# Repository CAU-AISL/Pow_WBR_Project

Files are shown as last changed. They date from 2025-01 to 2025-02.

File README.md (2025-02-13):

# WBR Control
**Wheeled Bipedal Robot POW** project for Capstone Design graduation thesis conducted. This project is inspired by [Ascento](https://www.youtube.com/@AscentoRobotics). @SeungbinOh, Jungbin Park, @Woodaengtang are contributors of this project. 

## Introduction
- This repository is including **ESP32 control** and **MATLAB simulation** code for wheeled bipedal robot POW.
- For robust behavior, balancing, velocity, yaw rate control were conducted using **LQR(Linear Quadratic Regulator)**.
- Discrete LQR gains were calculated offline with 10mm height interval.
- During HILS, LQR gain is determined using linear interpolation according to desired height.

## Library dependencies
- **ESP32 Board**
    - [arduino-esp32](https://github.com/espressif/arduino-esp32): 4D Systems gen4-ESP32 16MB Modules (ESP32-S3R8n16)
    - [Eigen](https://github.com/hideakitai/ArduinoEigen)
    - [Bolder Flight Systems SUBS](https://github.com/bolderflight/sbus)
    - [ESP32Servo](https://madhephaestus.github.io/ESP32Servo/annotated.html)

## Future scope of WBR
- **Backlash issues**
- **Autonomous driving**
- **Enhance estimation**
- **Task variation**
- **Upgrading hardware**
- **Extendable research topics**
    - Optimization based control
    - Reinforcement learning control
    - Autonomous navigation, SLAM
    - System ID - SINDy, Digital twin
    - Estimation in saturated measurement(Tobit Kalman filter)

## Hardware

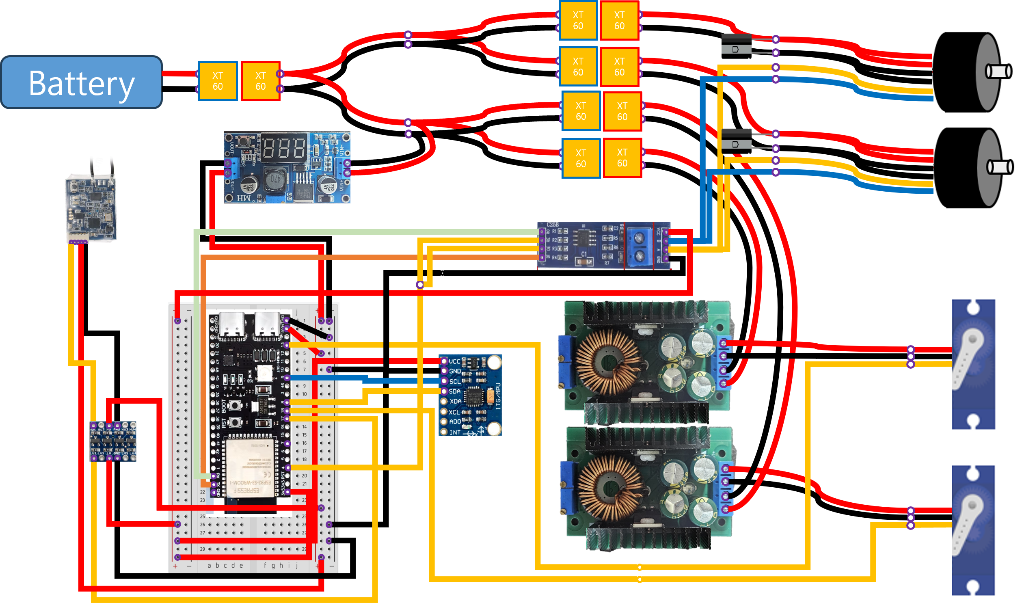
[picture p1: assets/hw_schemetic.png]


- [DCDC step down converter](https://ko.aliexpress.com/item/1005006295829518.html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)
- [DC-DC buck converter](https://ko.aliexpress.com/item/1005001711248152.html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)
- [ESP32 N16R8](https://ko.aliexpress.com/item/1005006002965361.html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) : Please do not use pin number 19 and 20. **Using 19, 20 pin causes serial monitor disconnection.**
- [Hip servo motor](https://ko.aliexpress.com/item/1005006086271452.html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)
- [Wheel motor](https://ko.aliexpress.com/item/1005006136735214.html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)
- [RC Receiver](https://ko.aliexpress.com/item/1005006821905179.html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)
- [MPU6050](https://ko.aliexpress.com/item/1005006579363624.html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)
- [TTL to RS485 converter](https://www.coupang.com/vp/products/104771330?itemId=317638085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)
- [Level shifter](https://www.coupang.com/vp/products/257783456?itemId=808722571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)

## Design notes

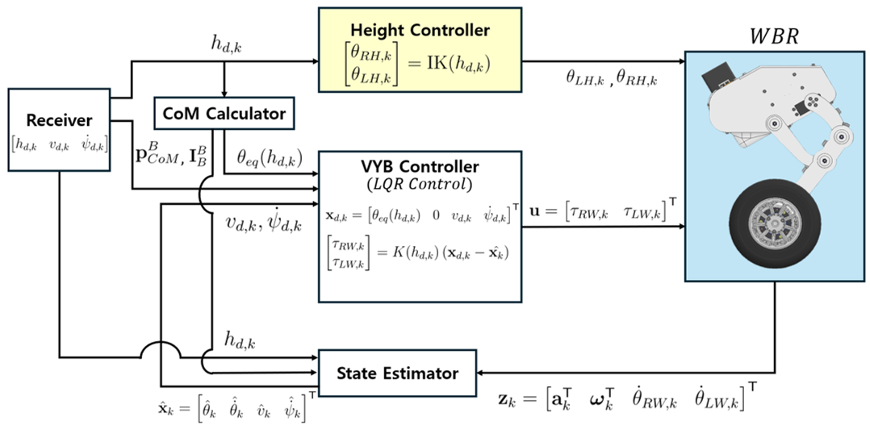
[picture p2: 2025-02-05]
assets/control_diagram.png

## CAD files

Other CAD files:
MATLAB/Linkage_Design/OldVersions/base.0001.ipt
MATLAB/Linkage_Design/OldVersions/link_l1.0001.ipt
MATLAB/Linkage_Design/OldVersions/link_l2.0001.ipt
MATLAB/Linkage_Design/OldVersions/link_l34.0001.ipt
MATLAB/Linkage_Design/OldVersions/linkage_system_sketch.0005.ipt
MATLAB/Linkage_Design/OldVersions/linkage_system_sketch_reference.0002.ipt
MATLAB/Linkage_Design/base.ipt
MATLAB/Linkage_Design/link_l1.ipt
MATLAB/Linkage_Design/link_l2.ipt
MATLAB/Linkage_Design/link_l34.ipt
MATLAB/Linkage_Design/linkage_system_sketch.ipt
MATLAB/Linkage_Design/linkage_system_sketch_reference.ipt
MATLAB/Linkage_Design/linkage_system_test.iam

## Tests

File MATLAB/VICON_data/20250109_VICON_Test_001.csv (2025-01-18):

Frame | Sub Frame | Position - WheeledBipedalRobot |  |  | Rotation (Helical) - WheeledBipedalRobot
 |  | TX | TY | TZ | RX | RY | RZ
Frames | Frames | mm | mm | mm | ° | ° | °
1 | 0 | 12.7373 | 648.974 | 259.901 | -1.66283 | -1.09888 | 1.52028
2 | 0 | 13.0095 | 648.28 | 260.051 | -1.9817 | -1.01025 | 1.58418
3 | 0 | 13.1938 | 647.962 | 260.054 | -2.1403 | -0.962508 | 1.56305
4 | 0 | 13.3098 | 647.865 | 260.017 | -2.19484 | -0.93518 | 1.53532
5 | 0 | 13.4157 | 647.948 | 259.977 | -2.18598 | -0.948337 | 1.47573
6 | 0 | 13.5538 | 647.663 | 260.082 | -2.34665 | -0.892663 | 1.5036
7 | 0 | 13.6543 | 647.708 | 260.1 | -2.34658 | -0.90425 | 1.44121
8 | 0 | 13.6985 | 647.693 | 260.108 | -2.38859 | -0.896542 | 1.39446
9 | 0 | 13.7813 | 647.774 | 260.112 | -2.37191 | -0.901932 | 1.36994
10 | 0 | 13.8433 | 647.807 | 260.074 | -2.40754 | -0.888137 | 1.34364
11 | 0 | 13.9018 | 647.842 | 260.05 | -2.42506 | -0.882477 | 1.35759
12 | 0 | 14.0122 | 647.935 | 260.056 | -2.42499 | -0.915033 | 1.36447
13 | 0 | 14.0654 | 647.981 | 260.091 | -2.42492 | -0.92564 | 1.35686
14 | 0 | 14.0829 | 648.054 | 260.089 | -2.40211 | -0.924017 | 1.33123
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

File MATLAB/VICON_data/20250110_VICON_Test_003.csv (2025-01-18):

Frame | Sub Frame | Position - WheeledBipedalRobot |  |  | Rotation (Euler Angle ZYX) - WheeledBipedalRobot
 |  | TX | TY | TZ | RX | RY | RZ
Frames | Frames | m | m | m | ° | ° | °
1 | 0 | -0.177393 | 0.611306 | 0.0641581 | -0.165102 | 1.92462 | 0.309445
2 | 0 | -0.177015 | 0.611374 | 0.0643333 | -0.152879 | 1.8503 | 0.317554
3 | 0 | -0.176653 | 0.611347 | 0.0644846 | -0.157014 | 1.78063 | 0.327459
4 | 0 | -0.176533 | 0.611347 | 0.0646045 | -0.155031 | 1.76415 | 0.344403
5 | 0 | -0.176532 | 0.611394 | 0.0646427 | -0.143893 | 1.77197 | 0.35604
6 | 0 | -0.176676 | 0.611202 | 0.0646261 | -0.178183 | 1.81013 | 0.372305
7 | 0 | -0.176701 | 0.611254 | 0.0645466 | -0.166321 | 1.83588 | 0.373788
8 | 0 | -0.176851 | 0.611213 | 0.0644148 | -0.171023 | 1.88289 | 0.368964
9 | 0 | -0.176971 | 0.611309 | 0.0642607 | -0.151127 | 1.92962 | 0.357114
10 | 0 | -0.177176 | 0.61138 | 0.0641004 | -0.13091 | 1.98978 | 0.357391
11 | 0 | -0.177305 | 0.611399 | 0.0639539 | -0.123309 | 2.03327 | 0.354787
12 | 0 | -0.177325 | 0.611407 | 0.0638758 | -0.119834 | 2.05503 | 0.356647
13 | 0 | -0.177246 | 0.611286 | 0.0638436 | -0.141933 | 2.05348 | 0.369164
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

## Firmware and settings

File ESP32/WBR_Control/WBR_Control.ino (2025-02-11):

#include "Params.h"
#include "Receiver.h"
#include "HRController.h"
#include "VYBController.h"
#include "MGServo.h"
#include "IMU.h"
#include "POL.h"
#include "EKF.h"
#include "CompenFilter.h"
#include "Logger.h"
#include "Timer.h"


// Properties와 Receiver, Controller 초기화
const Properties properties = createDefaultProperties();
POL Pol(properties);
HardwareSerial RS485(1);
MGServo ServoLW(1, RS485);
MGServo ServoRW(2, RS485);
Receiver receiver(Serial2);
IMU MPU6050;

HRController HR_controller;
VYBController VYB_controller(ServoRW, ServoLW);
EKF Estimator(Pol);
// CompenFilter Estimator(properties);

Logger WIFI_Logger(ssid, password);

Eigen::Matrix<float, 4, 1> x = Eigen::Matrix<float, 4, 1>::Zero();
Eigen::Matrix<float, 4, 1> x_d = Eigen::Matrix<float, 4, 1>::Zero();
Eigen::Matrix<float, 2, 1> u_prev = Eigen::Matrix<float, 2, 1>::Zero();
Eigen::Matrix<float, 2, 1> u = Eigen::Matrix<float, 2, 1>::Zero();
Eigen::Matrix<float, 8, 1> z = Eigen::Matrix<float, 8, 1>::Zero();
Eigen::Matrix<float, 2, 1> iq_vec = Eigen::Matrix<float, 2, 1>::Zero();

int i = 0;
Timer log_timer(Timer::TimerType::Millis);
Timer sampling_timer(Timer::TimerType::Millis);
Timer temp_timer(Timer::TimerType::Millis);
float h_d = HEIGHT_MAX, phi_d = 0;
float v_d = 0, dpsi_d = 0;

void serialPrintStates();

// ==============================================================================
//                                    SETUP
// ==============================================================================
void setup() {
  // Serial 통신, Receiver, HR Controller 초기화
  Serial.begin(115200);               // Serial 통신 시작
  receiver.begin();                            // Receiver 초기화
  HR_controller.attachServos(LH_PIN, RH_PIN);  // Servo Pin 설정

  // IMU (MPU6050) 초기화
  if (!MPU6050.begin()) {
    Serial.println("[ERROR] Fail to initialize IMU.");
  }

  // RS485 초기화
  pinMode(RS485_DE_RE, OUTPUT);                                         // RS485 방향 제어 핀 설정
  digitalWrite(RS485_DE_RE, LOW);                                       // RS485 수신 모드 설정
  RS485.begin(460800, SERIAL_8N1, RS485_RX_PIN, RS485_TX_PIN);  // RS485 통신 시작

  // WIFI 연결
  WIFI_Logger.begin();

  // PSRAM 상태 확인 및 초기화
  if (psramFound()) {
    Serial.println("PSRAM available.");
    if (!psramInit()) {
      Serial.println("PSRAM initialization failed!");
      while (1) {}  // 초기화 실패 시 무한 루프
    } else {
      Serial.println("PSRAM initialized successfully!");
    }
    Serial.printf("PSRAM size: %d bytes\n", ESP.getPsramSize());  // PSRAM 크기 출력
  } else {
    Serial.println("PSRAM not available.");
    while (1) {}  // PSRAM 미탐지 시 무한 루프
  }

  // SBUS 데이터 수신 대기 (타임아웃 처리)
  Timer receiver_timer(Timer::TimerType::Millis);
  receiver_timer.start();
  const unsigned long timeout = 5000;  // 타임아웃 5초 설정

  while (!receiver.readData()) {
    if (receiver_timer.getDuration() > timeout) {
      Serial.println("Timeout: No data received from SBUS.");
      receiver_timer.start();  // 타임아웃 초기화
    }
  }
  receiver.updateData();  // 데이터 업데이트

  // Logger pre-allocation ==============================================
  WIFI_Logger.readyToLogValue("cal_time");

  WIFI_Logger.readyToLogTimeStamp();  // 시간 기록
  // Desired states
  WIFI_Logger.readyToLogValue("h_d"); 
  WIFI_Logger.readyToLogValue("theta_d");
  WIFI_Logger.readyToLogValue("v_d");
  WIFI_Logger.readyToLogValue("psi_dot_d");
  
  // Estimated states
  WIFI_Logger.readyToLogValue("theta_hat");
  WIFI_Logger.readyToLogValue("theta_dot_hat");  // 시간 기록
  WIFI_Logger.readyToLogValue("v_hat");          // 시간 기록
  WIFI_Logger.readyToLogValue("psi_dot_hat");    // 시간 기록

  // Control inputs
  WIFI_Logger.readyToLogValue("tau_RW");  // 시간 기록
  WIFI_Logger.readyToLogValue("tau_LW");  // 시간 기록

  // Measurements
  WIFI_Logger.readyToLogValue("acc_x");
  WIFI_Logger.readyToLogValue("acc_y");  // 시간 기록
  WIFI_Logger.readyToLogValue("acc_z");  // 시간 기록
  WIFI_Logger.readyToLogValue("gyr_x");  // 시간 기록
  WIFI_Logger.readyToLogValue("gyr_y");
  WIFI_Logger.readyToLogValue("gyr_z");         // 시간 기록
  WIFI_Logger.readyToLogValue("theta_dot_RW");  // 시간 기록
  WIFI_Logger.readyToLogValue("theta_dot_LW");  // 시간 기록

  WIFI_Logger.readyToLogValue("current_RW");
  WIFI_Logger.readyToLogValue("current_LW");
  // =======================================================================

  // 시간 측정 시작
  log_timer.start();
  sampling_timer.start();
}

// ==============================================================================
//                                    LOOP
// ==============================================================================
void loop() {
  // sampling time이 경과했을 때만 실행
  if (sampling_timer.getDuration() >= dt * 1000) {
    // 경과 시간 출력
    Serial.print("SamplingTime(ms):");
    Serial.print(sampling_timer.getDuration());
    Serial.print(" ");

    sampling_timer.start();  // sampling timer 초기화


    if (receiver.readData()) {
      receiver.updateData();
    }

    if (receiver.isRun()) {
      // Running Mode
      //// update Pol state and input for EKF ////
      Pol.setState(x);
      // Pol.setInput(u);
      Pol.setInput(u_prev);  // u_k-2

      // measurement update
      MPU6050.readData();  // read k-th IMU measurements
      MPU6050.getIMUMeasurement(z);

      VYB_controller.sendReadStateCommand();  // read k-th motor speed
      VYB_controller.getMotorSpeedMeasurement(z);
      VYB_controller.getMotorCurrentMeasurement(iq_vec);

      //// state estimation ////
      if (!Estimator.estimate_state(x, z)) {
        // Diverge Safe Gaurd
        ServoLW.sendTorqueControlCommand(0);
        ServoRW.sendTorqueControlCommand(0);
        while (true) {
          Serial.println("Mass matrix Singularity Error. Change mode to Off Mode...");
          x.setZero();
          u.setZero();
          Estimator.reset_estimator();
          if (receiver.readData()) {
            receiver.updateData();
          }
          delay(500);
          if (!receiver.isRun()) {
            return;
          }
        }
      }

      //// Get Desired States from receiver ////
      receiver.updateDesiredStates();
      h_d = receiver.getDesiredHeight();
      // phi_d = receiver.getDesiredRoll();
      phi_d = 0;  // roll control disable
      v_d = receiver.getDesiredVel();
      dpsi_d = receiver.getDesiredYawVel();

      x_d.segment<2>(2) << v_d, dpsi_d;

      //// calculate CoM and Inertia from CoM Calculator ////
      Pol.setHR(h_d, phi_d);
      Pol.calculate_com_and_inertia();  // 여기서 inverse kinematics로 theta_hips도 계산됨
      Pol.get_theta_eq(x_d(0));         // update desired pitch angle with equilibrium point

      //// compute VYB controller gain ////
      VYB_controller.computeGainK(h_d);
      VYB_controller.computeInput(x_d, x);

      //// Send control command of HR controller and VYB controller
      HR_controller.controlHipServos(Pol.get_theta_hips());
      VYB_controller.sendControlCommand();
      u_prev = u;
      u = VYB_controller.getInputVector();

      //============= Logging ======================================================================
      // Logging calculating time and timestamp
      WIFI_Logger.logValue("cal_time", sampling_timer.getDuration());  // Log the calculating time
      WIFI_Logger.logTimeStamp(log_timer.getDuration());               // Log the current timestamp

      // Desired states (reference values for control)
      WIFI_Logger.logValue("h_d", h_d);           // Desired height
      WIFI_Logger.logValue("theta_d", x_d(0));    // Desired pitch angle (theta)
      WIFI_Logger.logValue("v_d", x_d(2));        // Desired velocity
      WIFI_Logger.logValue("psi_dot_d", x_d(3));  // Desired yaw rate (psi_dot)
      

      // Estimated states (current system state estimates)
      WIFI_Logger.logValue("theta_hat", x(0));      // Estimated pitch angle (theta)
      WIFI_Logger.logValue("theta_dot_hat", x(1));  // Estimated pitch rate (theta_dot)
      WIFI_Logger.logValue("v_hat", x(2));          // Estimated velocity
      WIFI_Logger.logValue("psi_dot_hat", x(3));    // Estimated yaw rate (psi_dot)

      // Control inputs (commands to the system)
      WIFI_Logger.logValue("tau_RW", u(0));  // Control torque for the right wheel (RW)
      WIFI_Logger.logValue("tau_LW", u(1));  // Control torque for the left wheel (LW)

      // Measurements (sensor readings)
      WIFI_Logger.logValue("acc_x", z(0));         // Acceleration in x-direction
      WIFI_Logger.logValue("acc_y", z(1));         // Acceleration in y-direction
      WIFI_Logger.logValue("acc_z", z(2));         // Acceleration in z-direction
      WIFI_Logger.logValue("gyr_x", z(3));         // Gyroscope reading in x-direction
      WIFI_Logger.logValue("gyr_y", z(4));         // Gyroscope reading in y-direction
      WIFI_Logger.logValue("gyr_z", z(5));         // Gyroscope reading in z-direction
      WIFI_Logger.logValue("theta_dot_RW", z(6));  // Angular velocity of the right wheel
      WIFI_Logger.logValue("theta_dot_LW", z(7));  // Angular velocity of the left wheel

      // Current measurements for the wheels
      WIFI_Logger.logValue("current_RW", iq_vec(0));  // Current for the right wheel
      WIFI_Logger.logValue("current_LW", iq_vec(1));  // Current for the left wheel
      //=============================================================================================
    } else if (receiver.isReset()) {
      // Estimator Reset
      x_d.setZero();
      VYB_controller.theta_d = 0.f;
      x.setZero();
      u.setZero();
      Estimator.reset_estimator();
      WIFI_Logger.resetLogData();
      log_timer.start();

    } else {
      // Off Mode
      ServoLW.sendTorqueControlCommand(0);
      ServoRW.sendTorqueControlCommand(0);
      u.setZero();

      WIFI_Logger.handleClientRequests();  // Log Data 전송

      Pol.setHR(h_d, phi_d);
      Pol.calculate_com_and_inertia();
      Pol.get_theta_eq(x_d(0));

      Pol.setState(x);
      Pol.setInput(u);

      // measurement update
      MPU6050.readData();
      MPU6050.getIMUMeasurement(z);
      VYB_controller.getMotorSpeedMeasurement(z);
      // state estimation
      if (!Estimator.estimate_state(x, z)) {
        // Diverge Safe Gaurd
        ServoLW.sendTorqueControlCommand(0);
        ServoRW.sendTorqueControlCommand(0);
        while (true) {
          Serial.println("Mass matrix Singularity Error. Change mode to Off Mode...");
          x.setZero();
          u.setZero();
          Estimator.reset_estimator();
          if (receiver.readData()) {
            receiver.updateData();
          }
          delay(500);
          if (!receiver.isRun()) {
            return;
          }
        }
      }

      // //============= Logging ======================================================================
      // // Logging calculating time and timestamp
      // WIFI_Logger.logValue("cal_time", sampling_timer.getDuration());  // Log the calculating time
      // WIFI_Logger.logTimeStamp(log_timer.getDuration());               // Log the current timestamp

      // // Desired states (reference values for control)
      // WIFI_Logger.logValue("h_d", h_d);           // Desired height
      // WIFI_Logger.logValue("theta_d", x_d(0));    // Desired pitch angle (theta)
      // WIFI_Logger.logValue("v_d", x_d(2));        // Desired velocity
      // WIFI_Logger.logValue("psi_dot_d", x_d(3));  // Desired yaw rate (psi_dot)

      // // Estimated states (current system state estimates)
      // WIFI_Logger.logValue("theta_hat", x(0));      // Estimated pitch angle (theta)
      // WIFI_Logger.logValue("theta_dot_hat", x(1));  // Estimated pitch rate (theta_dot)
      // WIFI_Logger.logValue("v_hat", x(2));          // Estimated velocity
      // WIFI_Logger.logValue("psi_dot_hat", x(3));    // Estimated yaw rate (psi_dot)

      // // Control inputs (commands to the system)
      // WIFI_Logger.logValue("tau_RW", u(0));  // Control torque for the right wheel (RW)
      // WIFI_Logger.logValue("tau_LW", u(1));  // Control torque for the left wheel (LW)

      // // Measurements (sensor readings)
      // WIFI_Logger.logValue("acc_x", z(0));         // Acceleration in x-direction
      // WIFI_Logger.logValue("acc_y", z(1));         // Acceleration in y-direction
      // WIFI_Logger.logValue("acc_z", z(2));         // Acceleration in z-direction
      // WIFI_Logger.logValue("gyr_x", z(3));         // Gyroscope reading in x-direction
      // WIFI_Logger.logValue("gyr_y", z(4));         // Gyroscope reading in y-direction
      // WIFI_Logger.logValue("gyr_z", z(5));         // Gyroscope reading in z-direction
      // WIFI_Logger.logValue("theta_dot_RW", z(6));  // Angular velocity of the right wheel
      // WIFI_Logger.logValue("theta_dot_LW", z(7));  // Angular velocity of the left wheel

      // // Current measurements for the wheels
      // WIFI_Logger.logValue("current_RW", iq_vec(0));  // Current for the right wheel
      // WIFI_Logger.logValue("current_LW", iq_vec(1));  // Current for the left wheel
      // //=============================================================================================

      serialPrintStates();
      // MPU6050.printData();
      Serial.println(" Off Mode");
    }
  }
}

void serialPrintStates() {
  Serial.print("theta:");
  Serial.print(x(0) * 180 / M_PI, 6);
  Serial.print(" ");
  Serial.print("theta_dot:");
  Serial.print(x(1) * 180 / M_PI, 6);
  Serial.print(" ");
  Serial.print("v:");
  Serial.print(x(2), 6);
  Serial.print(" ");
  Serial.print("psi_dot:");
  Serial.print(x(3) * 180 / M_PI, 6);
  Serial.print(" ");
  Serial.print("u_RW:");
  Serial.print(u(0), 6);
  Serial.print(" ");
  Serial.print("u_LW:");
  Serial.print(u(1), 6);
  Serial.print(" ");
}

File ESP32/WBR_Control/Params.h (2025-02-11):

#ifndef PARAMS_H
#define PARAMS_H

#include <math.h>
#include <ArduinoEigenDense.h>

// 단위 변환 매크로 함수
#define MM_TO_M(mm) ((mm)*1e-3)
#define G_TO_KG(g) ((g)*1e-3)
#define GMM2_TO_KGM2(gmm2) ((gmm2)*1e-9)

// BaudRate 설정
#define RS485_BAUDRATE 460800  // Motor와 같이 맞춰줘야함
#define SERIAL_BAUDRATE 115200

// 핀 번호 정의
#define LH_PIN 13  // 왼쪽 서보 핀
#define RH_PIN 21  // 오른쪽 서보 핀

#define SBUS_RX_PIN 15  // SBUS 수신 핀

#define RS485_DE_RE 1    // DE/RE 제어 핀
#define RS485_TX_PIN 40  // DI (TX) 핀
#define RS485_RX_PIN 42  // RO (RX) 핀

#define SDA_PIN 8   // SDA MPU6050 핀
#define SCL_PIN 17  // SCL MPU6050 핀

// 범위 설정 (height와 phi)
const float HEIGHT_MIN = 0.07;  // 최소 높이 (m)
const float HEIGHT_MAX = 0.2;   // 최대 높이 (m)

const float PHI_MIN = -15.0;  // phi 최소값 (degree)
const float PHI_MAX = 15.0;   // phi 최대값 (degree)

const float VEL_MAX = 1;     // 최대 속도 (m/s)
const float YAW_MAX = 1;  // 최대 yaw angular velocity (rad/s)

const float MAX_TORQUE_COMMAND = 100.000;  // 최대 torque command
// const float MAX_TORQUE = 0.12f;  // 최대 torque command
// const float MAX_TORQUE = 0.48f;  // 최대 torque command
const float MAX_TORQUE = 0.75f;  // 최대 torque command


// 핫스팟 정보 입력 -> 정보만 입력하면 와이파이 연결 된다.
// const char* ssid = "Jeongbin";       // 핫스팟 이름
// const char* password = "james0928";  // 핫스팟 비밀번호
// const char* ssid = "Woodaengtang";       // 핫스팟 이름
// const char* password = "jonghyun1234";  // 핫스팟 비밀번호

const char* ssid = "OSB";           // 핫스팟 이름
const char* password = "12345678";  // 핫스팟 비밀번호

const float dt = 0.008;  // sampling time
// const float dt = 0.007;  // sampling time


// mm -> m 단위 변환 함수 (벡터)
template<typename T>
Eigen::Matrix<T, 3, 1> mmToMVector(const Eigen::Matrix<T, 3, 1>& vec) {
  return vec * static_cast<T>(1e-3);
}

// gmm^2 -> kgm^2 단위 변환 함수 (행렬)
template<typename T>
Eigen::Matrix<T, 3, 3> gmm2ToKgm2Matrix(const Eigen::Matrix<T, 3, 3>& mat) {
  return mat * static_cast<T>(1e-9);
}

// Properties 구조체 정의
struct Properties {
  float a, b, l1, l2, l3, l4, l5, L, R;

  // 관성 및 질량 관련 변수들
  float m_Body;
  Eigen::Matrix<float, 3, 1> CoM_Body;
  Eigen::Matrix<float, 3, 3> I_Body;

  float m_TAR;  // Thigh Link Active Right
  Eigen::Matrix<float, 3, 1> CoM_TAR;
  Eigen::Matrix<float, 3, 3> I_TAR;

  float m_TAL;  // Thigh Link Active Left
  Eigen::Matrix<float, 3, 1> CoM_TAL;
  Eigen::Matrix<float, 3, 3> I_TAL;

  float m_TPR;  // Thigh Link Passive Right
  Eigen::Matrix<float, 3, 1> CoM_TPR;
  Eigen::Matrix<float, 3, 3> I_TPR;

  float m_TPL;  // Thigh Link Passive Left
  Eigen::Matrix<float, 3, 1> CoM_TPL;
  Eigen::Matrix<float, 3, 3> I_TPL;

  float m_CR;  // Calf Link Right
  Eigen::Matrix<float, 3, 1> CoM_CR;
  Eigen::Matrix<float, 3, 3> I_CR;

  float m_CL;  // Calf Link Left
  Eigen::Matrix<float, 3, 1> CoM_CL;
  Eigen::Matrix<float, 3, 3> I_CL;

  float m_RW;  // Wheel Right
  Eigen::Matrix<float, 3, 1> CoM_RW;
  Eigen::Matrix<float, 3, 3> I_RW;

  float m_LW;  // Wheel Left
  Eigen::Matrix<float, 3, 1> CoM_LW;
  Eigen::Matrix<float, 3, 3> I_LW;
};

// Properties 기본값 설정 함수
inline Properties createDefaultProperties() {
  Properties props = {
    0.075 * cos(M_PI / 6.0),  // a
    0.075 * sin(M_PI / 6.0),  // b
    0.106,                    // l1
    0.077,                    // l2
    0.050,                    // l3
    0.137,                    // l4
    0.008,                    // l5
    0.123,                    // L
    0.0725                    // R
  };

  // Mainbody
  // props.m_Body = G_TO_KG(1524.76209213f);  // G_TO_KG 함수에서 반환값이 float인 경우 f를 추가
  // props.CoM_Body = mmToMVector(Eigen::Matrix<float, 3, 1>(10.81299751f, -0.19574788f, 36.74451323f));
  // props.I_Body = gmm2ToKgm2Matrix((Eigen::Matrix<float, 3, 3>() << 4221074.20231635f, 26062.23004946f, 277168.19335956f,
  //                          26062.23004946f, 7437280.54727470f, 6416.10856472f,
  //                          277168.19335956f, 6416.10856472f, 8509987.98611482f)
  //                                   .finished());
  props.m_Body = G_TO_KG(1524.76209213f);  // G_TO_KG 함수에서 반환값이 float인 경우 f를 추가
  props.CoM_Body = mmToMVector(Eigen::Matrix<float, 3, 1>(13.71923256f, -0.22808627f, 34.91864017f));
  props.I_Body = gmm2ToKgm2Matrix((Eigen::Matrix<float, 3, 3>() << 4274811.10362144f, 21823.60087554f, 202865.50474913f,
                                   21823.60087554f, 7103674.50655196f, 7275.19023018f,
                                   202865.50474913f, 7275.19023018f, 8108785.33349067f)
                                    .finished());

  // Calf Link Left
  props.m_CL = G_TO_KG(319.23782393f);
  props.CoM_CL = mmToMVector(Eigen::Matrix<float, 3, 1>(172.54736867f, -3.72877629f, 7.27850779f));
  props.I_CL = gmm2ToKgm2Matrix((Eigen::Matrix<float, 3, 3>() << 101346.64715298f, -5353.69484487f, -27779.40548575f,
                                 -5353.69484487f, 703160.42663078f, -258.16665555f,
                                 -27779.40548575f, -258.16665555f, 676774.26748659f)
                                  .finished());
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

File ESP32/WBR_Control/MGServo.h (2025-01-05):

#ifndef MGSERVO_H
#define MGSERVO_H

#include <Arduino.h>
#include "Params.h"

// 명령어 및 응답 프레임의 길이 정의
constexpr uint8_t FRAME_COMMAND_LENGTH = 5;
constexpr uint8_t TORQUE_CONTROL_LENGTH = 2;
constexpr uint8_t SPEED_CONTROL_LENGTH = 4;
constexpr uint8_t READ_MOTOR_STATE2_LENGTH = 7;

// 명령어 타입 정의
constexpr uint8_t FRAME_HEAD = 0x3E;
constexpr uint8_t TORQUE_CONTROL_COMMAND = 0xA1;
constexpr uint8_t SPEED_CONTROL_COMMAND = 0xA2;
constexpr uint8_t READ_MOTOR_STATE2_COMMAND = 0x9C;

// MGServo 클래스 정의
class MGServo {
private:
  HardwareSerial& RS485;

  uint8_t motorID;
  int8_t temperature;  // temperature (℃)
  uint16_t encoder;
  int16_t iq_raw;     // raw current (LSD)
  int16_t speed_raw;  // speed raw (LSD)
  float iq;           // current (A)
  float speed;        // speed (deg/s)


public:
  MGServo(uint8_t motorID, HardwareSerial& RS485_ref)
    : motorID(motorID), RS485(RS485_ref) {
    temperature = 0;
    encoder = 0;
    iq_raw = 0;
    speed_raw = 0;
    iq = 0;
    speed = 0;
  }

  //////// Getter functions ////////////////
  uint8_t getMotorID() const {
    return motorID;
  }

  int8_t getMotorTemperature() const {
    return temperature;
  }

  uint16_t getMotorEncoder() const {
    return encoder;
  }

  int16_t getMotorIqRaw() const {
    return iq_raw;
  }

  float getMotorIq() const {
    return iq;
  }

  float getMotorSpeed() const {
    return speed;
  }
  ////////////////////////////////////////////

  // 토크 제어 명령 전송
  bool sendTorqueControlCommand(int16_t iqControl) {
    const size_t commandLength = FRAME_COMMAND_LENGTH + TORQUE_CONTROL_LENGTH + 1;      // frame + data + data_checksum
    const size_t responseLength = FRAME_COMMAND_LENGTH + READ_MOTOR_STATE2_LENGTH + 1;  // frame + data + data_checksum

    uint8_t command[commandLength];
    uint8_t response[responseLength];

    writeTorqueControlCommand(command, iqControl);  // command array에 command frame 작성
    sendCommand(command, commandLength);            // RS485를 통해 command 전송

    // RS485를 통해 response를 받고 response validation
    if (!readResponse(response, responseLength) || !validateResponse(response, responseLength)) {
      return false;
    }

    // response 정보를 통해 Motor state update
    extractReadState2Data(response);
    return true;
  }

  // 모터 상태 2 읽기 명령 전송
  bool sendCommandReadMotorState2() {
    const size_t commandLength = FRAME_COMMAND_LENGTH;                                  // frame + data + data_checksum
    const size_t responseLength = FRAME_COMMAND_LENGTH + READ_MOTOR_STATE2_LENGTH + 1;  // frame + data + data_checksum

    uint8_t command[commandLength];
    uint8_t response[responseLength];

    writeReadState2Command(command);      // command array에 command frame 작성
    sendCommand(command, commandLength);  // RS485를 통해 command 전송

    // RS485를 통해 response를 받고 response validation
    if (!readResponse(response, responseLength) || !validateResponse(response, responseLength)) {
      return false;
    }

    // response 정보를 통해 Motor state update
    extractReadState2Data(response);
    return true;
  }

  void printMotorState() const {
    Serial.print("Temperature(");
    Serial.print(motorID);
    Serial.print("):");
    Serial.print(temperature);
    Serial.print(" Encoder(");
    Serial.print(motorID);
    Serial.print("):");
    Serial.print(encoder);
    Serial.print(" Speed(");
    Serial.print(motorID);
    Serial.print("):");
    Serial.print(speed);
    Serial.print(" Current(");
    Serial.print(motorID);
    Serial.print("):");
    Serial.print(iq);
  }

private:

  // 토크 제어 명령 프레임 준비
  void writeTorqueControlCommand(uint8_t* command, int16_t iqControl) {
    prepareCommandFrame(command, TORQUE_CONTROL_COMMAND, TORQUE_CONTROL_LENGTH);
    command[FRAME_COMMAND_LENGTH] = iqControl & 0xFF;
    command[FRAME_COMMAND_LENGTH + 1] = (iqControl >> 8) & 0xFF;
    command[FRAME_COMMAND_LENGTH + 2] = calculateChecksum(&command[FRAME_COMMAND_LENGTH], TORQUE_CONTROL_LENGTH);
  }

  // 속도 제어 명령 프레임 준비
  void writeSpeedControlCommand(uint8_t* command, int32_t speedControl) {
    prepareCommandFrame(command, SPEED_CONTROL_COMMAND, SPEED_CONTROL_LENGTH);
    command[FRAME_COMMAND_LENGTH] = *(uint8_t*)(&speedControl);
    command[FRAME_COMMAND_LENGTH + 1] = *((uint8_t*)(&speedControl) + 1);
    command[FRAME_COMMAND_LENGTH + 2] = *((uint8_t*)(&speedControl) + 2);
    command[FRAME_COMMAND_LENGTH + 3] = *((uint8_t*)(&speedControl) + 3);
    command[FRAME_COMMAND_LENGTH + 4] = calculateChecksum(&command[FRAME_COMMAND_LENGTH], SPEED_CONTROL_LENGTH);
  }

  // 모터 상태 2 명령 프레임 준비
  void writeReadState2Command(uint8_t* command) {
    prepareCommandFrame(command, READ_MOTOR_STATE2_COMMAND, 0x00);
  }

  // 명령 프레임 준비
  void prepareCommandFrame(uint8_t* command, const uint8_t commandType, const uint8_t dataLength) {
    command[0] = FRAME_HEAD;
    command[1] = commandType;                    // 명령어 타입
    command[2] = motorID;                        // 모터 ID
    command[3] = dataLength;                     // 데이터 길이
    command[4] = calculateChecksum(command, 4);  // 체크섬 계산
  }

  // 모터 상태 2 데이터 추출
  void extractReadState2Data(const uint8_t* response) {
    temperature = (int8_t)response[FRAME_COMMAND_LENGTH];
    iq_raw = (int16_t)(response[FRAME_COMMAND_LENGTH + 1] | (response[FRAME_COMMAND_LENGTH + 2] << 8));
    iq = static_cast<float>(iq_raw) * 3.3 / 2048;
    speed_raw = (int16_t)(response[FRAME_COMMAND_LENGTH + 3] | (response[FRAME_COMMAND_LENGTH + 4] << 8));
    speed = static_cast<float>(speed_raw) / 10;
    encoder = (uint16_t)(response[FRAME_COMMAND_LENGTH + 5] | (response[FRAME_COMMAND_LENGTH + 6] << 8));
  }

  // 명령 전송
  void sendCommand(const uint8_t* command, const size_t commandLength) {
    // 송수신 버퍼 초기화
    while (RS485.available()) {
      RS485.read();  // 버퍼 비우기
    }

    // RS485 송신 모드로 전환
    toggleRS485Mode(HIGH);

    // 명령 전송
    RS485.write(command, commandLength);
    RS485.flush();  // 전송 완료 대기

    // RS485 수신 모드로 복귀
    toggleRS485Mode(LOW);
  }


  // 응답 읽기
  bool readResponse(uint8_t* response, const size_t responseLength) {
    toggleRS485Mode(LOW);

    unsigned long startTime = micros();  // 타이머 시작
    while (RS485.available() < responseLength) {
      if (micros() - startTime > 500) {
            Serial.println("[ERROR] Response timeout! No sufficient data received.");
            return false;  // 타임아웃 발생
        }
    }
    size_t bytesRead = RS485.readBytes(response, responseLength);

    if (bytesRead != responseLength) {
      Serial.print("[ERROR] Failed to read the full response! ");
      printInfo();
      return false;
    }

    return true;
  }

  // 응답 검증
  bool validateResponse(const uint8_t* response, size_t responseLength) const {
    if (calculateChecksum(response, 4) != response[4]) {
      Serial.print("[ERROR] Frame Checksum mismatch!");
      printInfo();
      return false;
    }
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

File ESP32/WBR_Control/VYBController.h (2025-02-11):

#ifndef VYB_CONTROLLER_H
#define VYB_CONTROLLER_H

#include <Arduino.h>
#include <ArduinoEigenDense.h>
#include "Params.h"
#include "MGServo.h"

/**
 * @class VYBController
 * @brief 제어 시스템의 LQR 기반 동작을 처리하는 클래스
 */
class VYBController {
private:
  MGServo& ServoRW;  ///< 우측 휠 서보
  MGServo& ServoLW;  ///< 좌측 휠 서보

  std::vector<Eigen::Matrix<float, 2, 4>> Ks;  ///< LQR 게인 행렬들의 벡터
  Eigen::Matrix<float, 2, 4> K;                ///< 현재 사용 중인 LQR 게인
  Eigen::Matrix<float, 2, 1> u;                ///< 제어 입력 벡터

  float iq_factor;        ///< 전류 변환 계수 (A/LSB)
  float torque_constant;  ///< 토크 상수 (Nm/A)
  float LW_factor = 0.001043224f;
  float RW_factor = 0.000857902f;

  float AngleFixRate = 0.1;

  float saturation;  ///< input saturation
  Eigen::Matrix<float, 2, 1> saturation_vec;
  const int RW_bias = 12;  ///< 우측 휠 모터의 바이어스 값

public:
  float theta_d;
  /**
   * @brief 생성자: VYBController 초기화
   * @param ServoRW_ 우측 휠 서보 객체 참조
   * @param ServoLW_ 좌측 휠 서보 객체 참조
   */
  VYBController(MGServo& ServoRW_, MGServo& ServoLW_)
    : ServoRW(ServoRW_), ServoLW(ServoLW_) {
    theta_d = 0.f;
    // 전류 및 토크 상수 초기화
    iq_factor = 0.001611328f;  // (A/LSB) 3.3 / 2048
    torque_constant = 0.7f;    // (Nm/A) * reduction ratio
    saturation = iq_factor * torque_constant * MAX_TORQUE_COMMAND;
    // saturation_vec << MAX_TORQUE_COMMAND * RW_factor, MAX_TORQUE_COMMAND * LW_factor;
    saturation_vec << MAX_TORQUE, MAX_TORQUE;


    // LQR 게인 초기화 (하드코딩된 데이터 삽입)
    Eigen::Matrix<float, 2, 4> mat;
    //////////////////////////////////////////////////////////
    mat << 1.35316904f, 0.14009245f, 0.23358589f, -0.12161902f,
      -1.36517013f, -0.14243867f, -0.23405192f, -0.12179830f;
    Ks.push_back(mat);

    mat << 1.40047216f, 0.14638508f, 0.23369175f, -0.12160757f,
      -1.41285639f, -0.14885450f, -0.23407320f, -0.12184087f;
    Ks.push_back(mat);

    mat << 1.44602994f, 0.15279748f, 0.23382116f, -0.12158976f,
      -1.45881851f, -0.15539539f, -0.23413544f, -0.12186834f;
    Ks.push_back(mat);

    mat << 1.48968650f, 0.15931475f, 0.23397350f, -0.12156787f,
      -1.50289679f, -0.16204545f, -0.23423617f, -0.12188368f;
    Ks.push_back(mat);

    mat << 1.53149557f, 0.16592279f, 0.23414424f, -0.12154222f,
      -1.54514525f, -0.16879039f, -0.23436934f, -0.12188799f;
    Ks.push_back(mat);

    mat << 1.57156576f, 0.17260877f, 0.23432853f, -0.12151281f,
      -1.58567342f, -0.17561742f, -0.23452873f, -0.12188200f;
    Ks.push_back(mat);

    mat << 1.61001973f, 0.17936153f, 0.23452203f, -0.12147964f,
      -1.62460463f, -0.18251548f, -0.23470875f, -0.12186644f;
    Ks.push_back(mat);

    mat << 1.64697959f, 0.18617179f, 0.23472118f, -0.12144289f,
      -1.66206114f, -0.18947534f, -0.23490463f, -0.12184212f;
    Ks.push_back(mat);

    mat << 1.68256117f, 0.19303219f, 0.23492316f, -0.12140290f,
      -1.69815838f, -0.19648966f, -0.23511244f, -0.12180996f;
    Ks.push_back(mat);

    mat << 1.71687199f, 0.19993741f, 0.23512588f, -0.12136017f,
      -1.73300286f, -0.20355303f, -0.23532897f, -0.12177102f;
    Ks.push_back(mat);

    mat << 1.75001117f, 0.20688435f, 0.23532789f, -0.12131532f,
      -1.76669221f, -0.21066222f, -0.23555173f, -0.12172640f;
    Ks.push_back(mat);

    mat << 1.78207150f, 0.21387275f, 0.23552830f, -0.12126915f,
      -1.79931713f, -0.21781670f, -0.23577883f, -0.12167735f;
    Ks.push_back(mat);

    mat << 1.81314599f, 0.22090653f, 0.23572687f, -0.12122289f,
      -1.83096725f, -0.22501991f, -0.23600886f, -0.12162555f;
    Ks.push_back(mat);

    mat << 1.84334794f, 0.22799757f, 0.23592427f, -0.12117958f,
      -1.86174765f, -0.23228239f, -0.23624048f, -0.12157472f;
    Ks.push_back(mat);
    /////////////////////////////////////////////////////////////////
  }

  /**
   * @brief 현재 제어 입력 벡터를 반환
   * @return Eigen::Matrix<float, 2, 1> u
   */
  Eigen::Matrix<float, 2, 1> getInputVector() {
    return u;
  }

  /**
   * @brief 모터 속도 측정을 수행하여 측정 벡터에 반영
   * @param z 모터 속도 측정값을 저장할 벡터
   */
  void getMotorSpeedMeasurement(Eigen::Matrix<float, 8, 1>& z) {
    z(6) = ServoRW.getMotorSpeed() * M_PI / 180;
    z(7) = ServoLW.getMotorSpeed() * M_PI / 180;
  }

  /**
  * @brief 모터 Current 측정값 update
  * @param iq_vec 모터 current 측정값을 저장할 벡터
  */
  void getMotorCurrentMeasurement(Eigen::Matrix<float, 2, 1>& iq_vec) {
    iq_vec << ServoRW.getMotorIq(), ServoLW.getMotorIq();
  }

  /**
   * @brief 현재 높이에 따라 LQR 게인 K를 계산
   * @param h 현재 높이 (m)
   */
  void computeGainK(const float h) {
    float temp = (h - HEIGHT_MIN) / 0.01;  // 구간을 10mm당 하나씩 나눔
    int idx = static_cast<int>(temp);      // 구간의 정수 인덱스 계산

    if (idx >= 0 && idx < static_cast<int>(Ks.size()) - 1) {
      // 보간 비율 계산
      float ratio = temp - idx;  // 현재 위치가 구간 내에서 차지하는 비율

      // 보간 수행
      K = Ks.at(idx) * (1.0f - ratio) + Ks.at(idx + 1) * ratio;
    } else if (idx < 0) {
      // h가 HEIGHT_MIN 이하일 경우 최소값 사용
      K = Ks.front();
    } else {
      // h가 범위를 벗어날 경우 최대값 사용
      K = Ks.back();
    }
  }

  /**
   * @brief 상태 벡터를 기반으로 제어 입력 벡터를 계산
   * @param x_d 목표 상태 벡터
   * @param x 현재 상태 벡터
   */
  void computeInput(Eigen::Matrix<float, 4, 1>& x_d, Eigen::Matrix<float, 4, 1>& x) {

    // if (x_d(0) - x(0) < 0) {
    //   theta_d -= AngleFixRate * dt;
    // } else {
    //   theta_d += AngleFixRate * dt;
    // }
    // x_d(0) = theta_d;

    u = K * (x_d - x);

    // // Input saturation
    // for (int j = 0; j < 2; j++) {
    //   if (u(j) > saturation) {
    //     u(j) = saturation;
    //   } else if (u(j) < -saturation) {
    //     u(j) = -saturation;
    //   }
    // }
    // Input saturation
    for (int j = 0; j < 2; j++) {
      if (u(j) > saturation_vec(j)) {
        u(j) = saturation_vec(j);
      } else if (u(j) < -saturation_vec(j)) {
        u(j) = -saturation_vec(j);
      }
    }
  }

  /**
   * @brief 계산된 제어 명령을 서보에 전송
   */
  void sendControlCommand() {
    // float u_RW = u(0) / (iq_factor * torque_constant);
    // float u_LW = u(1) / (iq_factor * torque_constant);

    // // Right Wheel motor의 마찰로 인해 발생하는 torque 문제를 조정해줌
    // if (u_RW < 0) {
    //   u_RW -= RW_bias;
    // } else if (u_RW > 0) {
    //   u_RW += RW_bias;
    // }

    float u_RW = u(0) / RW_factor;
    float u_LW = u(1) / LW_factor;

    ServoRW.sendTorqueControlCommand(static_cast<int16_t>(u_RW));
    ServoLW.sendTorqueControlCommand(static_cast<int16_t>(u_LW));
  }
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

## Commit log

2024-12-12 Good Case 1
2024-12-12 Demo case : Very good
2024-12-23 chore: Arduino codes moved
2024-12-23 chore: MATLAB codes moved
    [20241206_0315_logdata_withwheel_offset10.csv, 20241207_0123_logdata_withwheel_speed_iqvalue_offset10.csv, 20241207_0409_logdata_withwheel_torque_speed_iqvalue_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]
2024-12-23 IMU test
2024-12-24 Address WiFi Warning Issues
    [HRController.h, IMU.h, MGServo.h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]
2024-12-26 revise type bug : speed and iq return type (int to float)
    [MGServo.h]
2024-12-26 change inverse kinematics function private to public
2024-12-26 Good case
2024-12-26 ADD: FFT update
    [logdata_forward_backward.csv, logdata_forward_backward_soft.csv, logdata_forwardbackward_soft_2.csv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]
2024-12-26 update IMU.h : fix high pass filter
    [IMU.h]
2024-12-27 Working on Wheel_Test : Not completed
2024-12-27 Update WBR_Control : EKF - apply motor speed precision to covariance matrix, VYBController - change torque constant considering reduction ratio
2024-12-27 add Timer
2024-12-27 reduce sampling time : IMU clock rate 100kHz to 400kHz RS485 baudrate 115200bps to 460800bps apply ps_vector for logging : pre-allocating reduce logging time and can use approximately 10 mins
2024-12-27 update IMU.h : add DLPF setting code
2024-12-27 MATLAB : add motor test log
    [20241227_logdata_wheelmotor_torquetest_3ms.csv, 20241227_logdata_wheelmotor_torquetest_5ms.csv]
2024-12-27 motor torque test code
2024-12-27 feat: Apply all updates from Wheel_Test to WBR_Control
2024-12-27 feat: Change the order of motor speed measurements
2024-12-29 feat: update wheel_motor_torquetest plotter
2024-12-29 add motor gain tunning log
    [20241229_logdata_wheelmotor_torquetest_3ms_Kp100_Ki100.csv, 20241229_logdata_wheelmotor_torquetest_3ms_Kp100_Ki120.csv, 20241229_logdata_wheelmotor_torquetest_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]
2025-01-02 Just update
    [20241229_logdata_balancing test_50ms.csv, 20241229_logdata_balancing test_50ms_LPF10.csv, 20241230_logdata_balancing_test_10ms_LPF10_prevu.csv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]
2025-01-03 chore: changed lpf, hpf flow
2025-01-03 chore: compensation filter code merged by Woodaengtang
2025-01-04 Very Good Case : EFK gain tunning and LQR sampling time 0.1 => decrease gain => decrease vibration
    [20250104_logdata_EKF_LowGain.csv]
2025-01-13 choir: Update Convinient plotter in data_plotter and Read_VICON_data
    [20241227_logdata_wheelmotor_torquetest_3ms.csv, 20241227_logdata_wheelmotor_torquetest_5ms.csv, 20241229_logdata_wheelmotor_torquetest_3ms_Kp100_Ki100.csv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]
2025-01-14 choir: Filter_Test, Filter_Test_Revised plotter update
2025-01-15 choir: 8ms Gain success
    [20250114_logdata_EKF_HighGain.csv]
2025-01-16 chore: Make VICON and log Comparison code
    [20250115_VICON_Test_006_h200.csv, 20250115_VICON_Test_007_h130.csv, 20250115_VICON_Test_008_h70.csv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]
2025-01-19 ADD: Make System ID
    [20250117_SystemID_HardTerrain.csv, 20250117_SystemID_SoftTerrain.csv, 20250117_VICON_Test_010_Dynamictest_1.csv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]
2025-01-19 chore: change gain and maximum velocity
2025-02-01 useless commit for push
    [20250119_Ts500.csv]
2025-02-02 fix: address Serial Monitor Error cause - Fixed USB connection issue caused by using pin 20 (USB D+ pin) for PWM. Removed PWM functionality on pin 20 to restore stable USB communication.
    [IMU.h, Params.h, WBR_Control.ino]
2025-02-11 chore: Update dynamic properties, get vibration resolved logdatas (20250210) and change gain
    [20250209_EKFTunning_hardterrain.csv, 20250209_VICON_Test_EKF_Hard.csv, 20250209_static_high.csv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]
